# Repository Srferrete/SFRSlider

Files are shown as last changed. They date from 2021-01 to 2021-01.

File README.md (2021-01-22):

# SFRSlider
Motorized Camera Slider

He creado este pequeño slider para fotografía, sobre todo pensando en hacer timelapses. Se controla mediante nuestro telefono movil con bluetooth

Estamos ante una primera versión muy sencilla de un solo eje controlado por una app muy sencilla donde tenemos 3 parametros para indicar el tiempo que va a tardar nuestro slider en completar el recorrido. Un boton ON para comenzar el movimiento y un boton OFF para parar el recorrido. 

iré ampliando información en este repositorio, teneis tanto los archivos STL como el firmware como la APP para controlarlo.

IMPORTANTE!!! Ni en el video ni aqui se explica como configurar el modulo bluetooth, hemos seguido esta guía  --> https://cutt.ly/jjOta6g

Puedes ver el video del montaje, instalacion y uso en mi Canal de Youtube. https://youtu.be/2Y3kqopLcV4

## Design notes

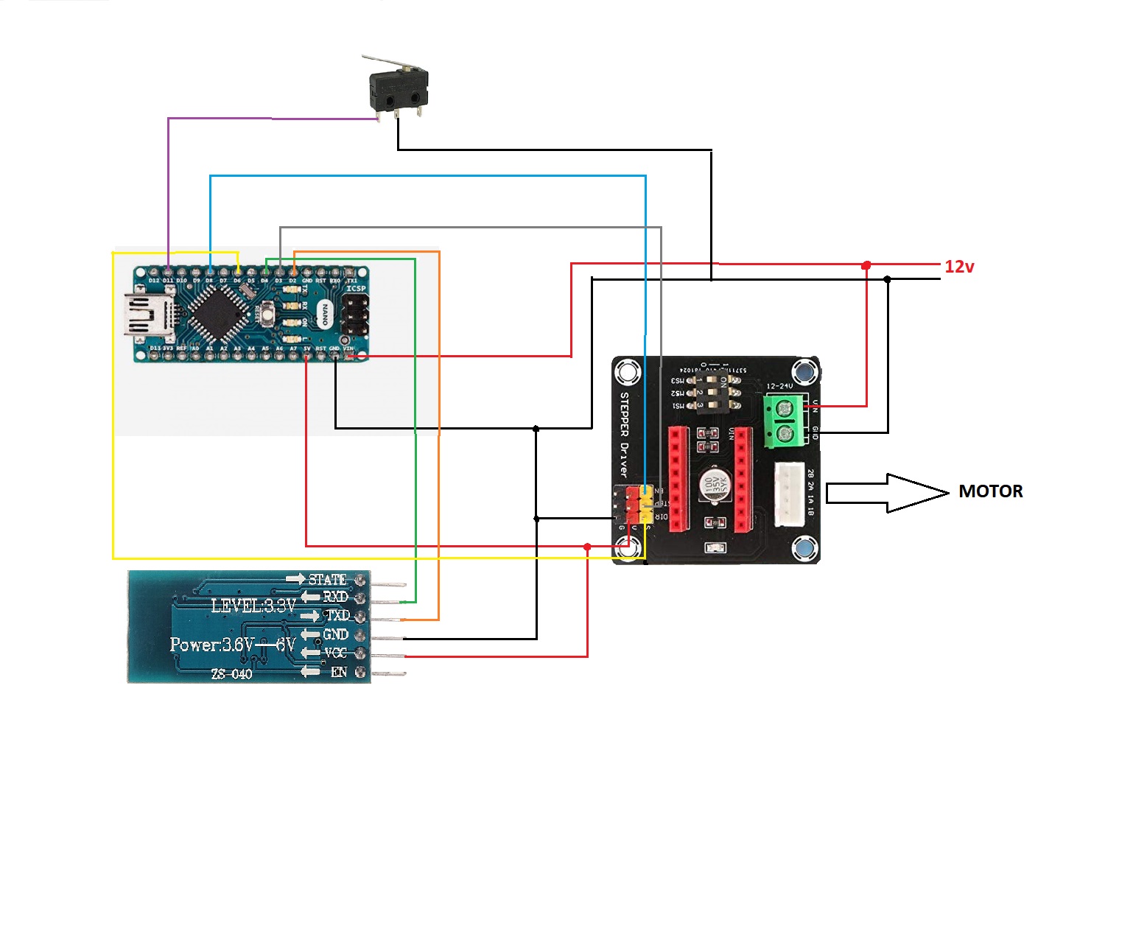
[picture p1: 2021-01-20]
Esquematico.jpg

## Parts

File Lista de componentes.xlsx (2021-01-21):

MATERIAL | CANTINDAD | ENLACE | NOTAS
PERGIL GSLOT 2040 1 METRO | 1 | https://www.makergal.es/product-page/perfil-gslot-2040-anodizado-natural
MOTOR PASO A PASO | 1 | https://amzn.to/3o6tNGl
ARDUINO NANO | 1 | https://amzn.to/3sH38U2
DRIVER A4988 | 1 | https://amzn.to/3iyzETC
SHIELD DRIVER | 1 | https://amzn.to/398kDFf
MODULO BLUETOOTH | 1 | https://amzn.to/3phdCHq
SET PIEZAS IMPRESAS | 1 | https://github.com/Srferrete/SFRSlider/tree/main/Stls
POLEA GT2 | 1 | https://amzn.to/3634zCq
POLEA LISTA M3 | 1 | https://www.makergal.es/product-page/polea-gt2-sincr%C3%B3nica-eje-3mm
CORREA GT2 | 3 METROS | https://amzn.to/3sKe3MH
RUEDAS GSLOT | 4 | https://www.makergal.es/product-page/ruedas-gslot
SEPARADOR EXCENTRICO | 2 | https://www.makergal.es/product-page/tuerca-excentrica
SEPARADOR 6MM | 2
ARDANDELAS M4 -1mm | 4
FINAL DE CARRERA | 1 | https://amzn.to/2KyGbBc
CABLES VARIOS |  | https://amzn.to/3iENUdB
CONECTOR DE CORRIENTE | 1
TRANSFORMADOR 12V - 2 AMP | 1 | https://amzn.to/3sLD7Tp
ROTULA PARA CAMARA | 1 | https://amzn.to/3p4A5aP
TORNILLO M5 X 12 | 4
TORNILLO M5 X 16 | 4
TORNILLO M5 X 30 | 4
TUERCAS M5 | 4
TUERCAS AUTOBLOCANTES M5 | 4
TORNILLO M3 X 16 | 1
TORNILLO M3X8 | 4
TUECA AUTOBLOCANTE M3 | 1
TUERCAS M4 | 7
TORNILLO M4 X10 | 5
TORNILLO M4 X ?? | 2

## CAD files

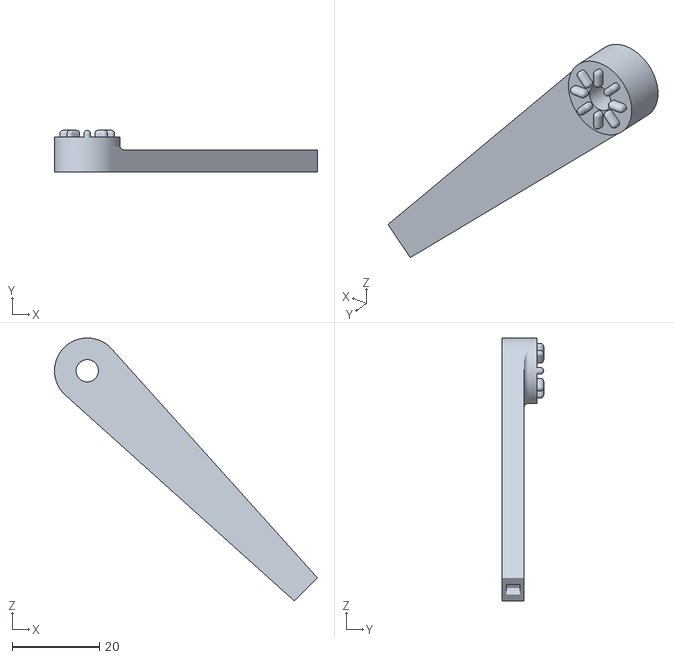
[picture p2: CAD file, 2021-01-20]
Stls/pata.stl
60.2 x 9.50 x 60.2

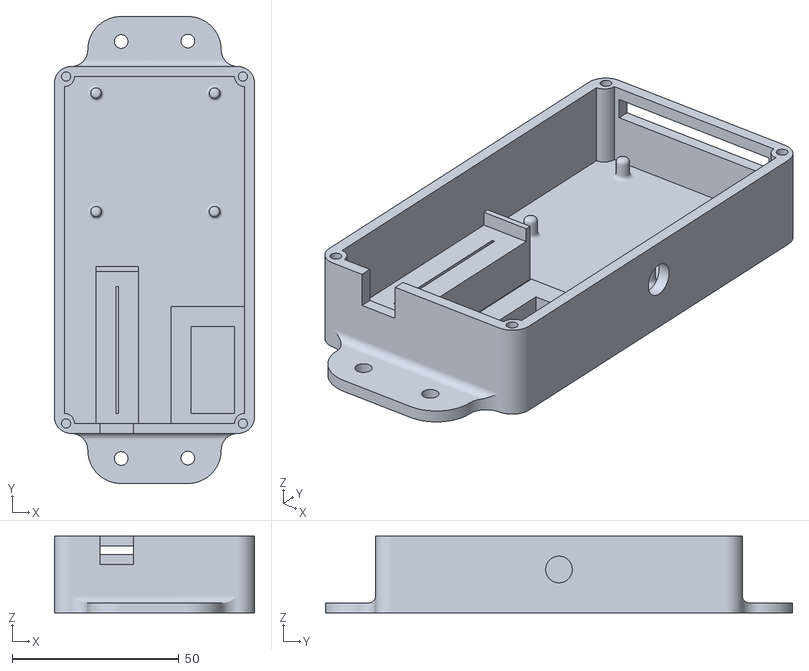
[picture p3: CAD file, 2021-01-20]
Stls/caja electronica.stl
60.0 x 140.0 x 23.0

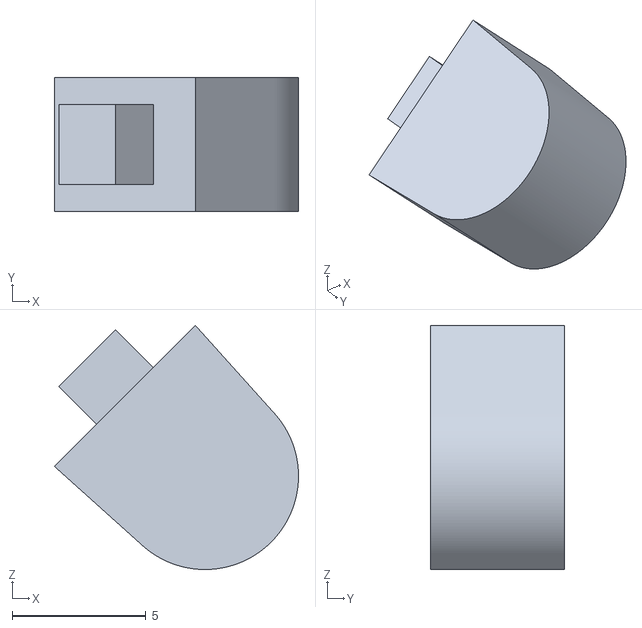
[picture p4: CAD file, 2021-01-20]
Stls/Pie de goma.stl
9.13 x 5.00 x 9.13

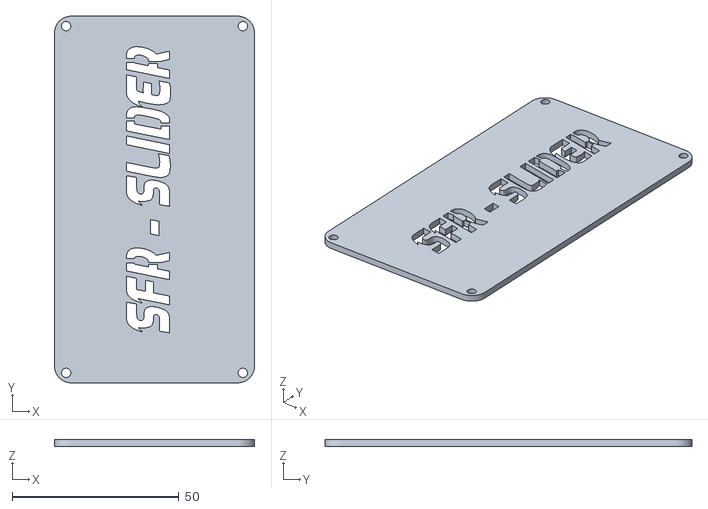
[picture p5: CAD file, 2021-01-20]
Stls/Tapa electronica.stl
60.0 x 110.0 x 2.00

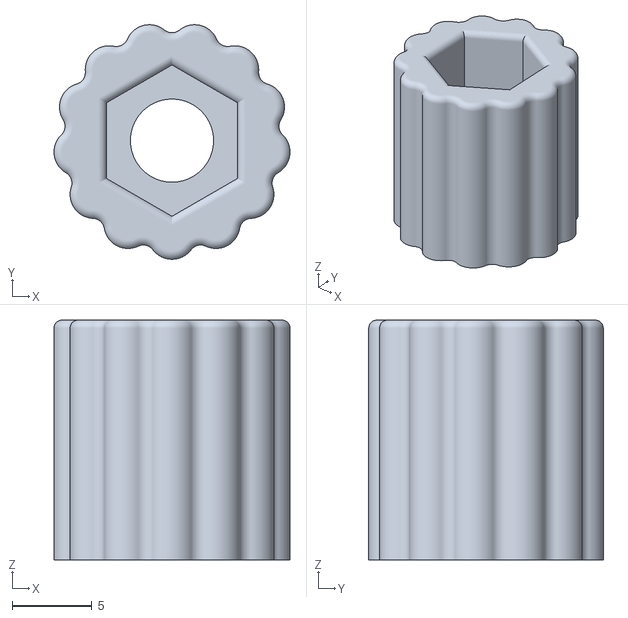
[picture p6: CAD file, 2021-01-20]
Stls/ruleta.stl
14.8 x 14.7 x 15.0

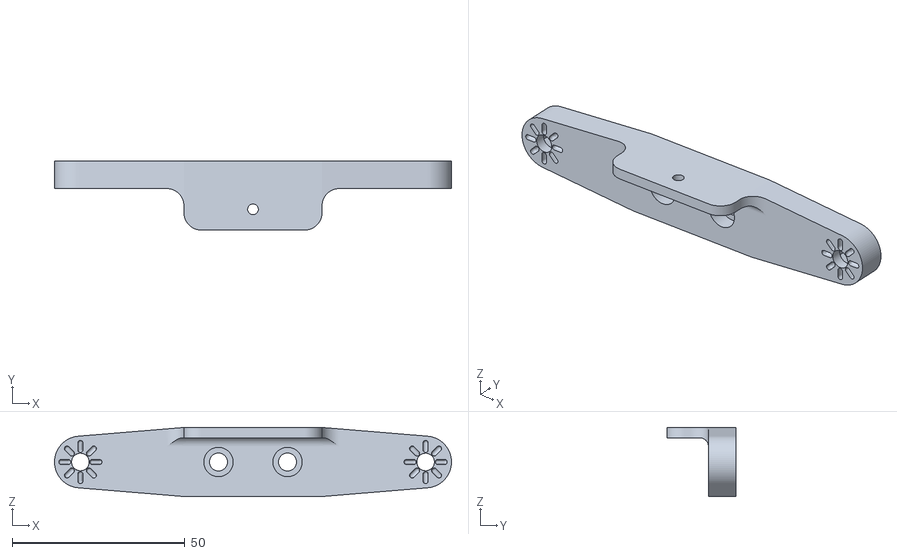
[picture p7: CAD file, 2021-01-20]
Stls/Lado polea.stl
115.0 x 20.0 x 20.0

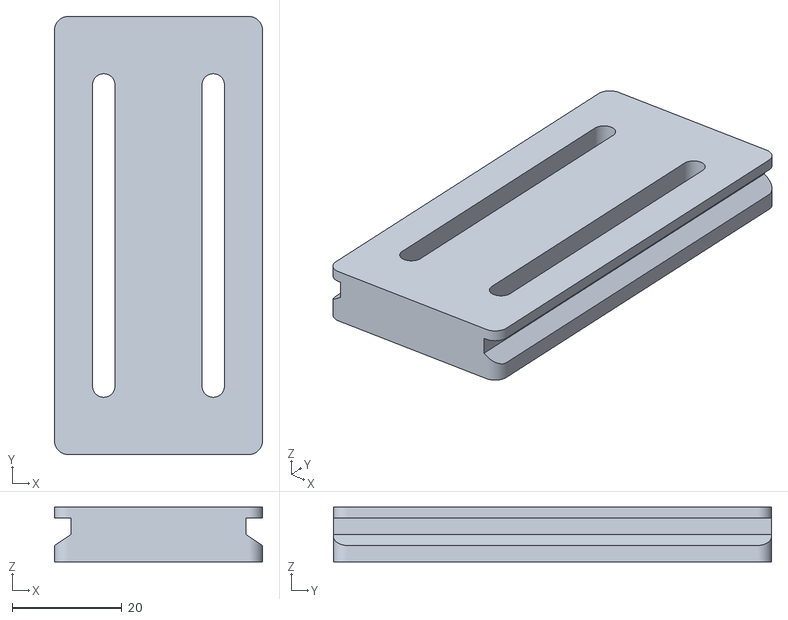
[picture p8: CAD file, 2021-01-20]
Stls/pastilla tripode.stl
38.0 x 80.0 x 10.0

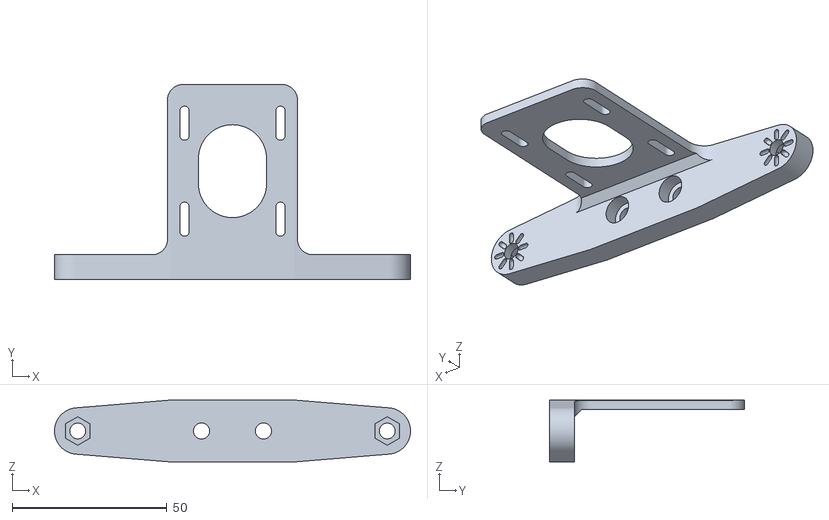
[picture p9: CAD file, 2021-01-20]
Stls/lado motor.stl
115.0 x 63.0 x 20.0

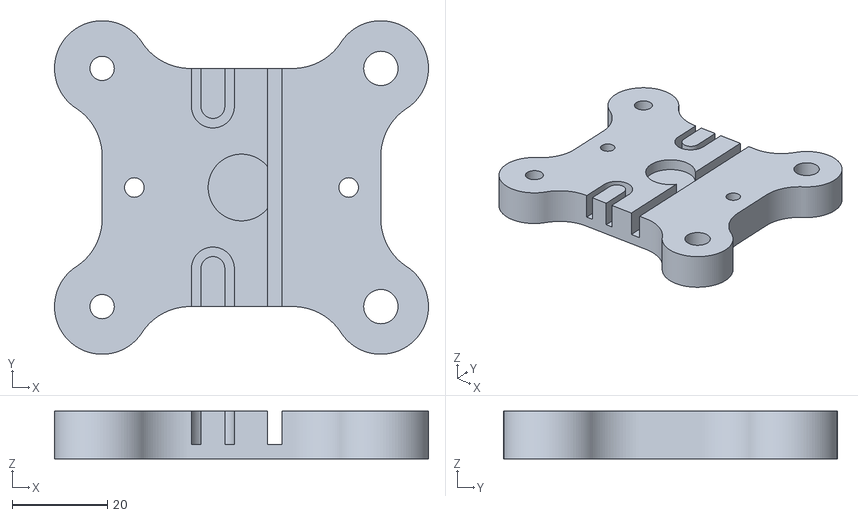
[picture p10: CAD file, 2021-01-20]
Stls/Carro.stl
78.5 x 70.0 x 10.0

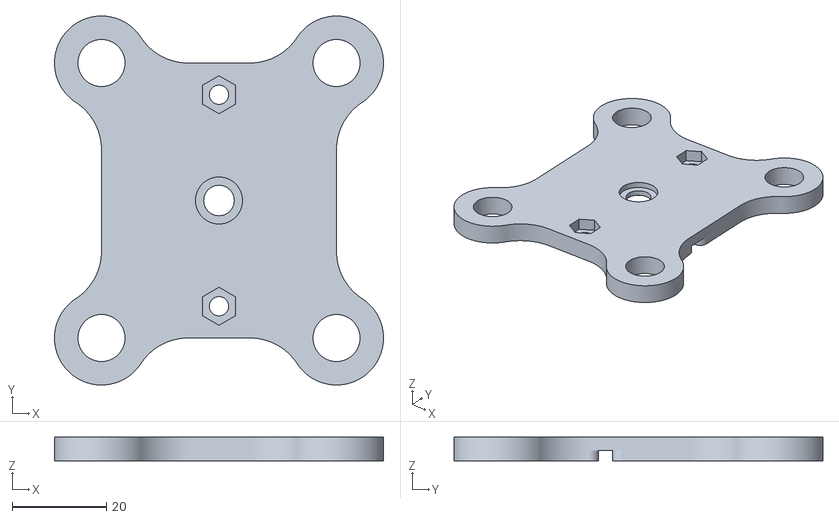
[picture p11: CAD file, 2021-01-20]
Stls/tapa carro.stl
70.0 x 78.5 x 5.00

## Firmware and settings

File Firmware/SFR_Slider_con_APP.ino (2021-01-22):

/***********************************************************SFRSlider**************************************************************/
/* Hemos creado este pequeño firmware para poder hacer funcionar nuestros slider con su APP Correspondiente
 *  de momento nuestro slider es de un solo eje y se mueve de inicio a fin en funcion del tiempo indicado
 *  la APP para android que hemos creado y que podeis descargar aquí--->
 *  Para ver el video del montaje y configutacion puedes ir a mi canal de Youtube--> https://youtu.be/2Y3kqopLcV4
 *  IMPORTANTE!!! Ni en el video ni aqui se explica como configurar el modulo bluetooth, hemos seguido esta guía  --> https://cutt.ly/jjOta6g
 *  La descarga de los ficheros STL para el montaje está Aquí -- >https://github.com/Srferrete/SFRSlider/tree/main/Stls
 *  Todo esto se ha creado bajo licencia https://creativecommons.org/licenses/by-nc/4.0/ compartir y dar reconocimiento a los creadores no cuesta nada, COMPARTE Y DISFRUTA
/***********************************************************SFRSlider**************************************************************/

/*LIBRERÍAS*/
#include <SoftwareSerial.h> // Librería que nos permite configurar un nuevo modulo de conexión
#include <AccelStepper.h> // Librería para el control de motores
/*FIN LIBRERIAS*/

/*DEFINICIONES*/
#define dirPin 6 //Pines para el motor
#define stepPin 3
#define enablePin 8
#define FCpin 11 //Pin para el final de carrera
#define motorInterfaceType 1 //Indicamos a la librería accelstepper que estamos usando un driver

#define STEPS 51950 // son los pasos totatel que tiene que dar el motor para completar el recorrido.

/*CALCULO DE PASOS DE TU SLIDER*/ /*IMPORTANTE*/
//Lo primero es medir el recorrido de nuestro eje, para un perfil de 750mm se quedan habiles 650mm de recorrido.
// Nuestro motor es de 200 pasos, con el microstep a 1/16 nos deja 3200 posos para cada vuelta del motor
// Nuestra polea es Gt2 de 20 dientes, 20 x 2mm (separacion entre dientes) nos da como resultado que nuestro eje se va a mover 40mm en cada vuelta
// si nuestro recorrido es 650mm divido 40mmm, nos da el numero de vueltas que tiene que dar el motor para el recorrido completo es decir 16.25 vueltas
// multiplicamos el nuemero de vueltas x los pasos, es decir, 16.25 * 3200 = 52000 pasos, obtenemos el numero total de pasos que tiene que dar el motor  para completar el recorrido.
// ponemos algun paso menos, para evitar que el carro choque al final. en este caso 51950
/*FIN CALCULO DE PASOS*/

SoftwareSerial BT(4,2); // definimos un nuevo serial y le asignamos los pines (RX,TX)
AccelStepper stepper = AccelStepper(motorInterfaceType, stepPin, dirPin); // Creamos una instancia de AccerStepper
/*FIN DEFINICIONES*/

/*VARIABLES*/
int val; // variable para el control de los pulsadores de la APP
int horas; // variables para el tiempo
int minutos;
int segundos;
int Ttotal; // Tiempo total pasado a segundos.
long int Vel = 0; // velocidad del slider, se expresa en pasos por segundo.
/*FIN VARIABLES*/

/*SETUP*/
void setup() {
  //Serial.begin(9600); // Inicializamos la comunicacion serie por USB
  BT.begin(9600); // Inicializamos la comunicacion serie por Bluetooth
  /*setup Motor*/
  pinMode(FCpin, OUTPUT); // Configuramos los pines.
  pinMode(enablePin, OUTPUT);
  digitalWrite(FCpin, HIGH);
  stepper.setMaxSpeed(4000); // seteamos la velocidad maxima de nuestro slider.

  homing(); // mandamos el carro al punto de origen
}
/*FIN SETUP*/

/*LOOP*/
void loop() {

    while (BT.available()>0)
    {
        val = BT.parseInt(); // Metemos cada valor de la APP en una variable y lo transformamos a entero
        horas = BT.parseInt(); 
        minutos = BT.parseInt(); 
        segundos = BT.parseInt(); 
 
        //Cuando lea el carácter fin de línea ('\n') quiere decir que ha finalizado el envío de los tres valores y si se recibe un 1, hemos pulsado el boton estar y comienza el recorrido
        if (BT.read() == '\n'&& val == 1  )
        {
          Ttotal= (horas*3600)+(minutos*60)+segundos; //pasamos todo a segundos
          Vel = STEPS/Ttotal; //Calculamos la velocidad que se expresa en pasos por segundos 
          //Serial.println(horas); // para debug
          //Serial.println(minutos);
          //Serial.println(segundos);
          //delay(500);
         // Serial.println(Ttotal);
          //val=5;
          slider();
        }
        
        if(val == 0){
          //homing();
          //Serial.println("HAS PULSADO CANCEL");
        }
       
    }
        
}
/*FIN DEL LOOP*/

/*FUNCIONES*/
void homing(){
    while(digitalRead(FCpin) == HIGH){ // Mientras el final de carrera no esté pulsado va a mover el motor hacie el punto de inicio.
    digitalWrite(enablePin,LOW); 
    stepper.setSpeed(-1500);
    stepper.runSpeed();
   }
   digitalWrite(enablePin,HIGH);
   stepper.setCurrentPosition(0); // después de hacer homing indicamos que el slider está en la posición 0
   val=0;
   horas,minutos,segundos = 0; //ponemos todo a 0 y estamos listo para comezar el recorrido
   //Serial.println(val);
   //delay(5000);
}

void slider(){
  digitalWrite(enablePin,LOW);
  while(stepper.currentPosition() != STEPS){ // va a mover el motor hasta que se completen todos los pasos
    stepper.setSpeed(Vel); // seteamos la velocidad en funcion de los valores introducidos en la app
    stepper.runSpeed(); // arrancamos el recorrido
    //Serial.println(stepper.currentPosition());
    if (BT.read() == '0' ){ // si pulsamos el boton OFF de la app interrumpe el recorrido
      //homing();
      break;
    }
  }
  horas,minutos,segundos = 0; //ponemos todo a 0
  homing(); // llamamos a la funcion homing para que el slider vuelva al principio 
}
/*FIN FUNCIONES*/
